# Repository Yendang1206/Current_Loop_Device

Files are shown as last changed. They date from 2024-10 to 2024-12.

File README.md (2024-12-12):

# Digital Current Loop Device for Frequency Converters
This repository contains the design and implementation details of a digital current loop device for frequency converters, developed as part of a thesis project. This device serves as an intermediate unit between a motor and a frequency converter, featuring advanced functionalities such as fast and slow increments or decrements for user-friendly control.
## Overview
The digital current loop device converts digital inputs—representing torque (0–50 Nm) and speed (0–3000 rpm)—into 0–20 mA analog current loops. This project integrates hardware and software to achieve precise control, accurate signal processing, and robust performance in noisy environments.
## Key Features
+ Converts torque and speed inputs from a rotary encoder into 0–20 mA current loop outputs.
+ Displays real-time input values on an LCD I2C screen.
+ Offers convenient fast/slow increment and decrement control.
+ Incorporates grounding, shielding, and paired signal wiring to enhance signal stability.
## The work methods
The work methods for this project were split into three main stages: 
 + circuit design, simulation and prototyping,
 + developing an Arduino software program,
 + manufacturing the physical Printed Circuit Boards (PCB).
## Results
Demonstrated positive correlation between torque and speed inputs with the corresponding current loop values (0–20 mA).
Achieved consistent performance between breadboard prototypes and integrated PCB systems.
Eliminated capacitive crosstalk and frequency interference using proper grounding, shielding, and CAT6 cable pairing.
## How to use
1. Connect the device between the motor and the frequency converter.
2. Adjust torque and speed inputs using the rotary encoder.
3. Monitor real-time input values on the LCD I2C display.
4. Verify current loop outputs using multimeters for accuracy.
## Future recommendations
Conduct EMC testing to further enhance noise immunity and long-term stability.

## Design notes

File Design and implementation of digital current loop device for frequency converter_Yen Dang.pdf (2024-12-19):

Yen Dang

# DESIGN AND IMPLEMENTATION

# OF DIGITAL CURRENT LOOP DEVICE

# FOR FREQUENCY CONVERTER

School of Technology
2024

VAASAN AMMATTIKORKEAKOULU
UNIVERSITY OF APPLIED SCIENCES Information Technology

ABSTRACT

Author | Yen Dang
Title | Design and Implementation of Digital Current Loop
| Device for Frequency Converter
Year | 2024
Language | English
Pages | 49
Name of Supervisor Jani Ahvonen

This thesis focuses on the design and implementation of a digital current loop device for a frequency converter to serve as an intermediate device between the motor and the frequency converter. In addition, this current loop device has an advanced feature of fast and slow increments or decrements, which is very convenient and user-friendly for users.

The work methods for this project were split into three main stages: circuit design and prototyping, Arduino software development and manufacturing the physical Printed Circuit Boards (PCB) for the digital current loop device. The expected inputs such as torque (Nm) and speed (rpm) values were fed into a rotary encoder and were displayed on an LCD I2C screen simultaneously. Then, the digital inputs for the torque (0 – 50 Nm) and for the speed (0 – 3000 rpm) were converted into the 0 – 20 mA current loops through DACs connected to the Arduino Nano board. In addition, the prototype measurement was divided into four main parts: Filter, Digital Signal Processing, Digital Analog Converter (DAC) and Analog to Digital Converter (ADC). These individual circuits on breadboards were verified with the software program simultaneously to achieve the accurate outcomes before integrating them together.

The results from the integrated PCBs were consistent with the individual circuit initially tested on the breadboards. Consequently, the desired torque and speed values showed positive correlations with the corresponding current values ranging from 0 – 20 mA. The finished device was assembled by placing PCBs into two metal boxes connected via CAT6 cable. To ensure accuracy and eliminate the capacitive crosstalk issue and frequency interference, signal wires were paired and proper grounding and shielding techniques were implemented. These measures were crucial for maintaining signal stability in potentially noisy environments, ultimately enhancing the accuracy of the 0 – 20 mA current loop outputs.

Keywords | Encoder, LCD I2C, Arduino Nano, DAC, current loop, ADC, digital
| current loop device, frequency converter

CONTENTS

6 TESTING AND TROUBLESHOOTING THE PROTOTYPE ON BREADBOARDS ..... 32

8.2 Comparative Analysis of Output Results of Ten Devices and Main

LIST OF TABLES

Table 1. Encoder logic state | 16
Table 2. Lookup table of the encoder changes | 28
Table 3. Error measurement range for actual current values | 43

LIST OF FIGURES

Figure 1. The hardware block diagram | 7
Figure 2. The flowchart software diagram | 8
Figure 3. Quadrature output table | 15
Figure 4. The external voltage circuit drawn in LTspice | 17
Figure 5. Simulation of the external voltage from the TL431 chip | 18
Figure 6. The simplified transmitter circuit drawn in LTspice | 20
Figure 7. Simulation of the simplified transmitter circuit | 20

Figure 8. The simulating receiver and feedback loop circuits drawn in LTspice. . 21

Figure 9. Simulation of the simulating receiver and feedback loop circuits | 22
Figure 10. The filter circuit’s schematic | 23
Figure 11. The main board circuit’s schematic | 24
Figure 12. The encoderLCD circuit’s schematic | 25
Figure 13. The appropriate libraries | 25
Figure 14. The calibrations for ADC and DAC for both channels | 26

Figure 15. Updating the torque and speed changes through the function of void

write_dac(float torque, int rpm) | 26
Figure 16. The state of a push-button | 27
Figure 17. The state of the encoder changes as an external interrupt | 27
Figure 18. Fast or slow increments featuring for four steps forward | 29
Figure 19. Safety checks within defined limits | 29
Figure 20. Open loop error check featuring | 30
Figure 21. I2C network | 31

Figure 21. The main components of the prototype testing on breadboards....... 32

Figure 23. The filter’s PCB | 34

Figure 29. Setup for testing the finished device with the frequency converter... 40

Figure 31. EMI shielding tapes applied to the CAT6 cable and EMC conductors

### 1 INTRODUCTION

The objective of the thesis is to design and implement a digital 0 – 20 mA device

for frequency converter. Users can adjust the expected values such as torque and

speed values on an LCD by rotating an encoder. The design of this device is illus-

trated through hardware and software diagrams.

### 1.1 Block Hardware Diagram

The hardware block diagram of the device is designed as shown below.

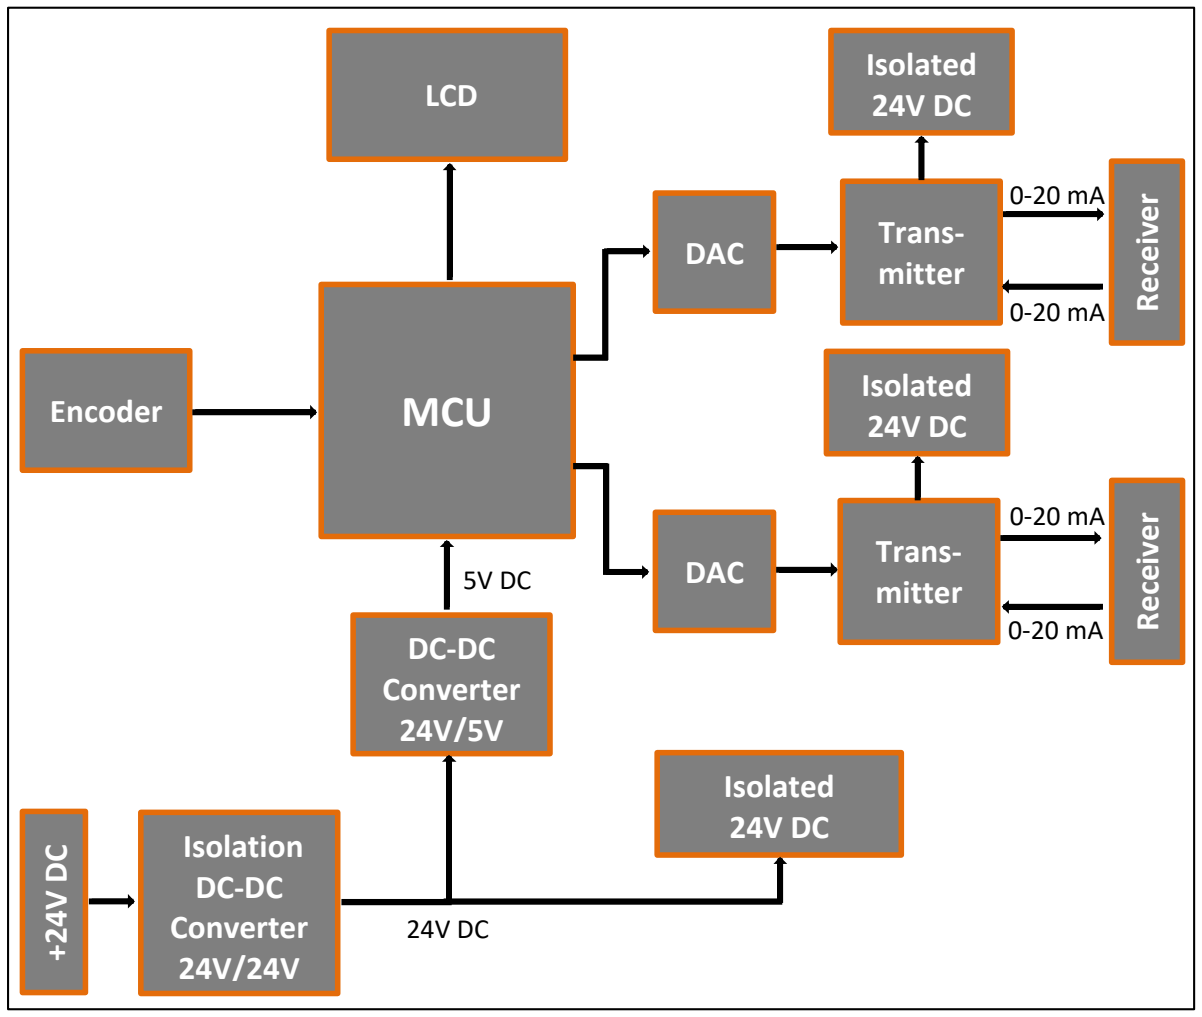
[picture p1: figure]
MCU; Trans- mitter; Encoder; DC-DC Converter 24V/5V; Isolation DC-DC Converter 24V/24V; DAC; LCD; Receiver Receiver; Isolated 24V DC

Figure 1. The hardware block diagram

Shown in the diagram, the encoder would be used to set the desired current value

by users. The desired digital value would be fed into MCU. Then, MCU would pro-

cess the data by displaying it on the LCD screen. MCU would send the desired dig-

ital value to a DAC. The DAC would convert the digital data back into the analog format. The analog output from DAC would control the current levels in the cur-

rent loops (transmitter and receiver).

### 1.2 Flowchart Software Diagram

The program for the device is presented in Figure 2.

Figure 2. The flowchart software diagram.

The main loop comprisesfive functionssuch as reset watchdog, check errors, write

text and values to LCD, write values to DACs and print all values to terminal. Each

of these fuctions has the specific internal behaviour within the system. The reset

watchdog serves as a critical safety mechanism by periodically resetting the watchdog timer to prevent the system from freezes or hangs, thus ensuring con-

tinuous operation. It acts as a fail-safe to automatically restart the system if it be-

comes unresponsive. Next, the check errors function continuously monitors the

system for any potential errors by comparing the desired torque and rpm values

with their corresponding ADC feedback. It returns a combined error code: 1 for a

torque channel error, 2 for an rpm channel error, or 3 if both channels have errors.

Another crucial function is the write text and values to LCD, which updates the

user interface by displaying relevant errors, torque, and rpm values on the LCD

screen. It provides users with real-time information about the system's status and

operation. Furthermore, the write values to DACs function converts digital signals

to analog outputs through DACs. It calculates new DAC values when the changes

occur, then updates the appropriate channels based on the values of the global

DAC_select variable. Lastly, the print all values to terminal function outputs all rel-

evant system values and information to a terminal interface. It is essential for de-

bugging and monitoring purposes, allowing users or operators to access detailed

system data in real-time.

### 2 REQUIREMENT SPECIFICATION

### 2.1 Functional Requirements

For the current control, the desired current level is adjusted within the range of 0

– 20 mA by turning the knob of the encoder.

For LCD screen, it should display the desired current level adjusted by users.

For the response time, the device should have a fast response time to quickly and

accurately adjust the current level.

### 2.2 Requirements for Interfaces

As for the user interface, the device should contain the LCD display and the rotary

encoder, which can be used to display and turn a knob to achieve the expected

digital values, respectively.

For hardware interface, the device should be able to rotate the encoder manually

to achieve the desired values displayed on the LCD display. Additionally, the device

contains two current loop outputs that can be directly connected to the analog

inputs of a frequency converter. The use of current loop outputs enables for pre-

cise control and communication between the device and the converter, allowing

real-time data transmission for adjusting accurate parameters such as torque and

speed.

For software interface, the device should allow users to control torque and speed

value setpoints. Moreover, the device should have a function to detect errors

when any open loops occur.

In terms of communication, the device could be programmed via serial communi-

cation through MCU’s USB port. This allows the MCU to transfer data to the com-

puter. The serial communication port is fixed, so there is no need to modify the

setting.

### 2.3 Other Requirements

### 2.3.1 Performance Requirements

There are some requirements for the device’s performance, as follows:

- Resolution of measurement: 0.02 mA
- Range of measurement: 0 – 20 mA

### 2.3.2 Usability Requirements

The device should have a user-friendly design, without the requirements for any

specialized skills.

### 2.3.3 Safety Requirements

The device must be protected with a fuse to prevent damage from overcurrent or

electrical faults.

### 2.3.4 Maintenance Requirements

The maintenance requirements include a more robust and user-friendly digital 0 –

20 mA device that can be monitored remotely and facilitates efficient trouble-

shooting and repairs if needed. This approach would help users to ensure its long-

term system performance and reliability, reduce the risk of unexpected outputs as

well.

### 2.3.5 Portability and Compatibility Requirements

Frequency converters play a crucial role in a variety of fields in daily life such as

control systems, power electronics, robotics, and automation, so the digital cur-

rent loop device would be used with various types of frequency converters. There-

fore, both portability and compatibility characteristics should be considered.

- For the portability factor, the designed device should be lightweight and

small for ease of installation.

- For the compatibility element, the digital current loop device could be able

to communicate with different types of communication interfaces when

integrated with a wide range of frequency converters.

### 2.3.6 Environmental Requirements

The device must operate within the temperature range from −30°C to +30°C to

ensure the desired functionality.

Furthermore, the device must operate its own environment as designed. Moreo-

ver, the device must comply with proper EMC regulations to minimize any poten-

tial interferences and noise.

### 2.4 Restrictions of Design

### 2.4.1 Restrictions caused by previously used technologies

The device must be very simple, so it can use MCU Arduino Nano A000005 board

schematic as a basic of design /3/.

The digital 0 – 20 mA device requires the existing industrial systems and control

devices to have the 0 – 20 mA input terminals. This is because in the real world,

the 0 – 20 mA or 4 – 20 mA current loops have commonly used as the standard for

signal transmission and electronic control in many industries /16/.

### 2.4.2 Hardware Limitations

The physical device should be as small as possible.

With a 0 mA current signal, it might be difficult to detect the system failures /14/.

Moreover, the wire loop distance between the transmitter and the receiver should

be within 500 meters.

### 2.4.3 Software Restrictions

The software for this project would be written in the C language, so only the GCC

C-compilers are permitted for developing this program.

### 2.4.4 Other Limitations

The power consumption should be minimized as much as possible while ensuring

the whole system has sufficient power to operate smoothly.

In addition, ground loops might be an unpredictable problem to crash the system.

This is because when many grounded devices placed in different locations are in-

tegrated with each other, which might have different voltage potentials, the noise

injection generated from their ground connection might affect grounded devices.

Therefore, we assumed all grounded components would be placed at the same

ground point to prevent the ground loops /15/.

### 3 OVERVIEW OF FREQUENCY CONVERTERS

A frequency converter is known as a variable frequency drive or adjustable speed

drive, which is used for modifying and controlling the speed and torque of electric

motors. Initially, this device converts the alternating current (AC) voltage into di-

rect current (DC) voltage. Then, it reconverts this DC back into AC with adjustable

frequency and the levels of voltage. This process allows for precise control over

the motor’s performance, enabling it to operate at the desired torque and rota-

tional speed required for the motor.

In addition, frequency converters can reduce motor power consumption by up to

50%, leading to significant energy savings. Moreover, they can collect motor data

such as temperature and vibrations via sensors, enabling condition monitoring and

preventive maintenance. This allows for remote operation monitoring and trou-

bleshooting through cloud solutions. Therefore, these advantages make frequency

converters essential devices in modern industrial applications, offering improved

performance, efficiency and control across a wide range of sectors.

However, frequency converters can create different kinds of interference when

assembled directly to motors or connected via cables. This includes acoustic noise,

harmonic reactions on the network, and electromagnetic compatibility (EMC)

noise, which can affect radio devices and data transfers. Therefore, the installation

of frequency converters and motors should address and manage noise and inter-

ference by complying with EMC requirements /12/.

### 4 BACKGROUND THEORY

### 4.1 Digital Signal Processing

In the implementation of the digital current loop device, we manipulate the digital

desired inputs from the rotary encoder and then convert them to analog signals

for transmission to the frequency converter. To ensure accurate tracking and fa-

cilitate real-time adjustments, we have integrated an I2C LCD 1602 display in this

project. This display serves as a visual interface, presenting the desired digital in-

put signals in a clear and easily readable format, allowing for quick identification

of any discrepancies or issues that may arise during operation. Therefore, this fea-

ture is useful for users to monitor the system's performance continuously when

there are any changes in the wanted digital inputs from the encoder.

### 4.1.1 Rotary Encoder

In the project, the rotary encoder is an incremental encoder, which is PEC11R-

4220F-S0024. This encoder converts angular motion or position of a shaft into an

analog or digital code to determine position or motion /8/. This encoder creates a

specified number of pulses per rotation. There are two output channels of pulses

such as Channel A and Channel B, which are offset from each other to indicate the

direction of rotation. The phase relationship between these channels is known as

quadrature. When the encoder is rotated in a clockwise direction (CW), Channel A

is leading Channel B in the output signal sequence. In contrast, during counter-

clockwise (CCW) rotation, the signal sequence reverses, meaning Channel B is

leading Channel A. The quadrature output table is represented as below /6/.

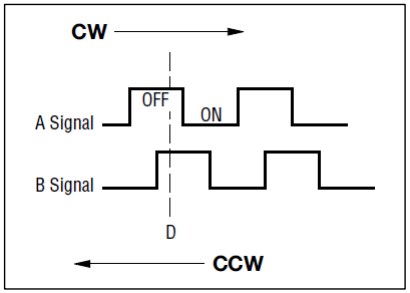
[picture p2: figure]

Figure 3. Quadrature output table.

Based on the quadrature output table, we could derive a encoder logic state table,

which is illustrated as Table 1.

Table 1. Encoder logic state.

Clockwise Direction

Position | Channel A | Channel B
1 | 0 | 0
2 | 1 | 0
3 | 1 | 1
4 | 0 | 1

In addition, this encoder is integrated with an additional feature, which is a push

switch option. The push button is often used to trigger of specific actions or toggle

between different operational modes.

### 4.1.2 I2C LCD1602

An I2C LCD1602 is a display device that combines a standard LCD (Liquid Crystal

Display) and an I2C (Inter-Integrated Circuit) module attached to its backside. This

device could show text and characters on 2 rows with 16 columns. One of the key

advantages of the I2C LCD1602 lies in its simplified connection interface. Unlike

traditional LCDs that often require multiple pins for operation, this device utilizes

only four pins: GND (ground), VCC (power supply), SDA (Serial Data), and SCL (Se-

rial Clock). This configuration simplifies the wiring process /5/.

### 4.2 Digital-Analog Converter

The Digital-Analog Converter (DAC) is a device that converts a digital input signal

into an analog output signal. Specifically, the DAC transforms the binary signal in

the form of bits into an analog voltage or current. The DACs find widespread ap-

plicationsin various digital signal processing fields, including audio amplifier, video

encoder, display electronics, data acquisition systems and motor control /7/.

In this thesis, we utilized two DFRobot Gravity 12-Bit I2C DAC modules equipped

with EEPROM (Electrically Erasable Programmable Read-Only Memory) to facili-

tate the conversion of digital input signalsfrom the encoder into voltage or current

signals suitable for the frequency converter. These DAC modules incorporate a 12-

bit DAC MCP4725 chip,support a wide input voltage range of 3.3 – 5 V and include

an I2C address selection switch. The integration of EEPROM in these DAC modules

significantly enhances data retention and system reliability. This non-volatile

memory component could retain the DAC input values while the power is turned-

off and resume the DAC output upon power resumption /7/.

Moreover, the input voltage for DAC modules was chosen at 5 V. Instead of using

the internal voltage of Arduino Nano, we chose for an external voltage circuit, aim-

ing for more stable and precise values for the whole system. Therefore, we used

the reference chip of TL431, namely Adjustable precision Zener shunt regulator,

to generate a constant output voltage at 5 V, a reference voltage for both DACs

and Arduino Nano. The circuit of the external voltage was designed in LTspice, as

shown in Figure 4.

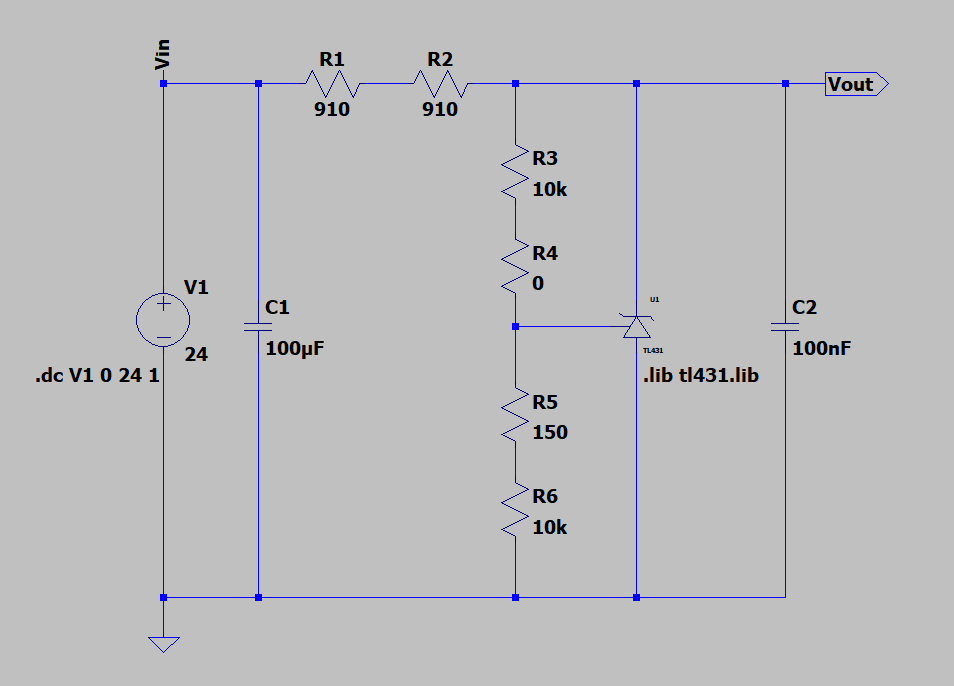
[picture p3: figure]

Figure 4. The external voltage circuit drawn in LTspice.

The circuit was then simulated as shown in the picture below. The results indicated

that the input voltage of 24 V, serving as the voltage source, was successfully con-

verted to the constant output voltage of 5 V.

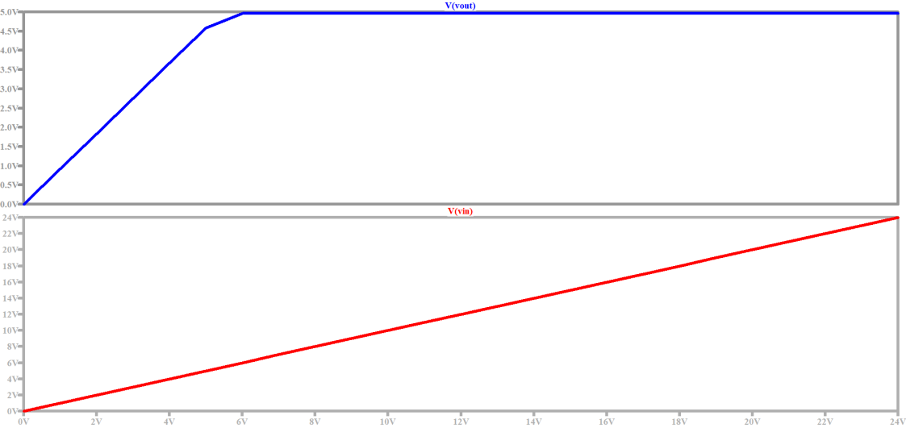
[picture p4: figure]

Figure 5. Simulation of the external voltage from the TL431 chip.

### 4.3 Current Loop

### 4.3.1 Transmitter Circuit

After converting the digital input signals to the analog signals, we connected the

analog output to a transmitter circuit for converting the input voltage into an out-

put current. The transmitter circuit incorporates two key components: an opera-

tional amplifier (LM324) and a transistor (BC547).

The LM324 operational amplifier was utilized for maintaining signal integrity and

ensuring that even small voltage changes are accurately represented in the output

current. The LM324 series feature cost-effective quad operational amplifiers with

true differential inputs, designed for single supply operation within a 3.0 – 32 V

range. The amplifier offerslow quiescent currents and numerous advantages such

asshort-circuit protection, true differential input stages. Moreover, the LM324 se-

ries also provides low input bias currents, internal compensation, and a common

mode range extending to the negative supply. With industry-standard pinouts and

ESD (Electrostatic Discharge) protection, these versatile amplifiers suit various ap-

plications requiring reliable operation /13/.

Following the amplifying stage, we used the BC547 Bipolar Junction Transistor

(BJT), which is used for amplifying current or switching. The transistor has three

regions: emitter, base, and collector. By controlling the base current, the transistor

can be turned on or off, allowing a larger current to flow between the collector

and emitter. This property makes it useful for amplifying small signals or acting as

a switch. The BC547 is popular due to its affordability, availability, and ease of use

/10/. Hence, this BC547 was used to generate the 0 – 20 mA output current in our

device.

The simplified transmitter circuit applied in this project in Figure 6.

Figure 6. The simplified transmitter circuit drawn in LTspice.

In addition, we also simulated the transmitter circuit above to measure the output

current of transmitter and the output voltage of receiver. After simulating, within

the input voltage range of 0 – 5 V, the transmitter output current was from 0 mA

to 20 mA and the receiver output voltage was from 0 V to 5 V. These results were

shown in Figure 7 below.

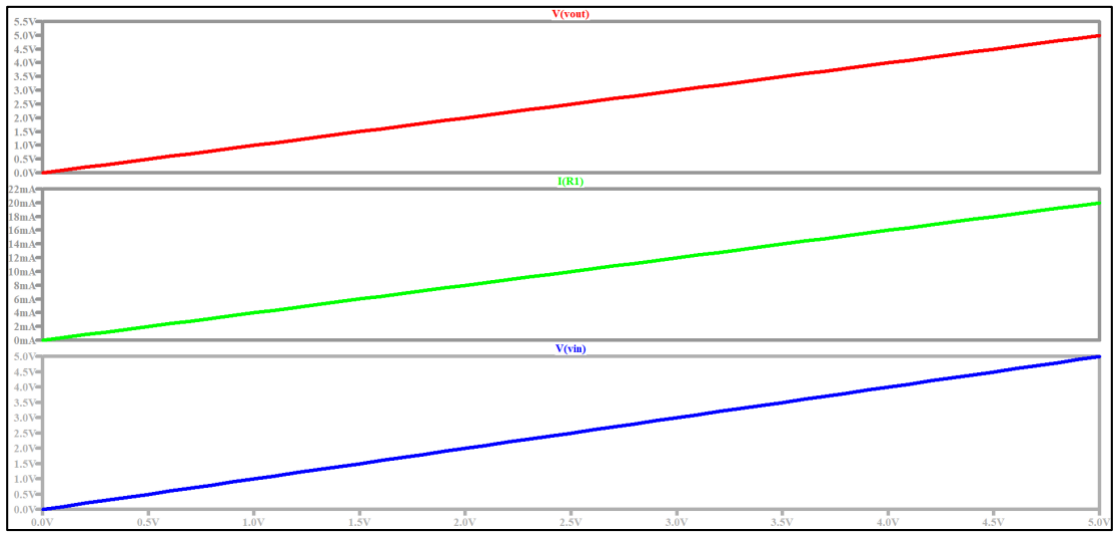
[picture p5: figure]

Figure 7. Simulation of the simplified transmitter circuit.

### 4.3.2 Feedback Loop Circuit

To complete the current loop, we implemented a feedback loop circuit designed

to capture and process the transmitted current signal. This circuit performs the

essential function of converting the received current back into its original voltage

form, enabling further processing or utilization of the signal. This circuit consisted of two main parts such as a resistor of 250 Ohm simulating frequency converter or

receivers and the feedback loop. To be specific, the feedback loop incorporated

three main parts: the low pass filter cut-off frequency, two diodes of 1N4148 for

ESD protection and a resistor of 250 Ohm.

Firstly, the low pass filter part consisted of a resistor of 10 kOhm, and a capacitor

of 100 nF for filtering out frequencies above the cut-off point. The cut-off fre-

quency was calculated following the below formula:

fc =

1
2πRC =

1
2π ∗ 10kΩ ∗ 100nF = 159.1 Hz ≈ 0.16 kHz

This calculated cut-off frequency of approximately 0.16 kHz ensured that the cir-

cuit effectively attenuates signals above this threshold, resulting in a more stable

output signal.

Secondly, these diodes of 1N4148 acted as a safeguard, protecting the sensitive

components of the circuit from potentially damaging voltage spikes that might oc-

cur due to static electricity or other sources.

Lastly, the receiver circuit included the resistor of 250 Ohm to control and main-

tain the targeted current output signals, preserving the 0 – 20 mA current flow

transmitted from the transmitter circuit and the receiver.

Here is the simulating receiver (the resistor of 250 Ohm) and feedback loop circuit

shown as below.

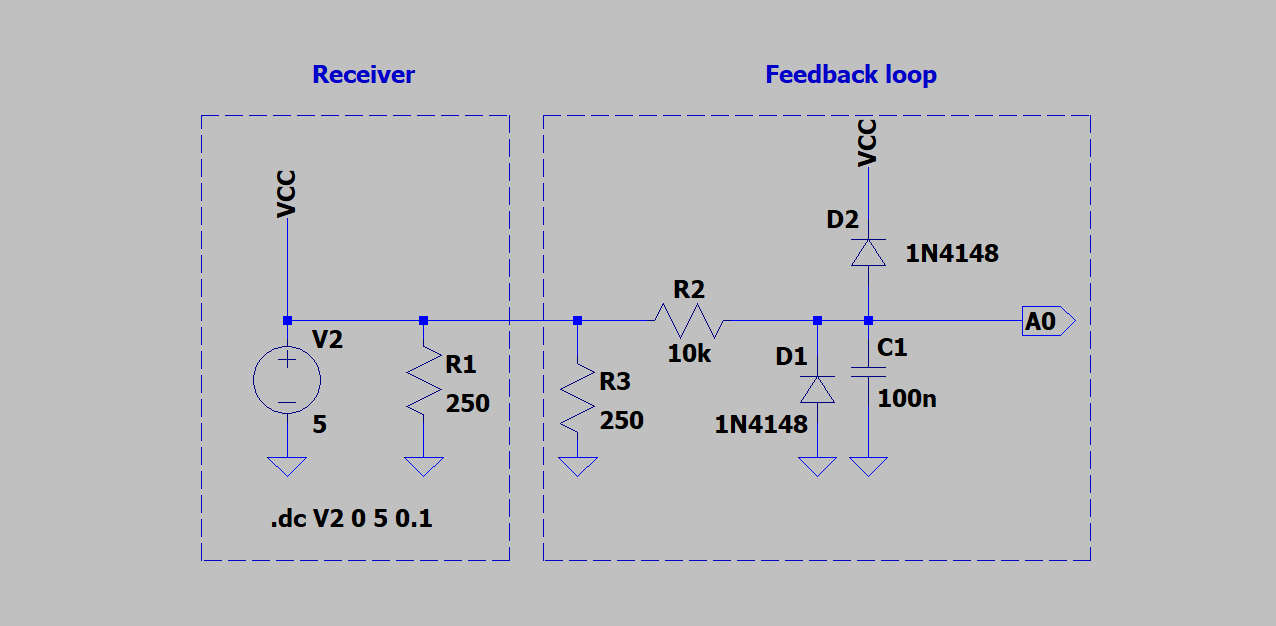
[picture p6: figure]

Figure 8. The simulating receiver and feedback loop circuits drawn in LTspice.

The simulation results from this simulating receiver and feedback loop circuits

were shown as Figure 9 below. The figure illustrated that the current value going

through R1 represented as the receiver or the frequency converter was from 0 –

20 mA. In addition, the 0 – 20 mA current flow was transmitted to the feedback

loop. Then, this current flow was converted into the output voltage of 5 V.

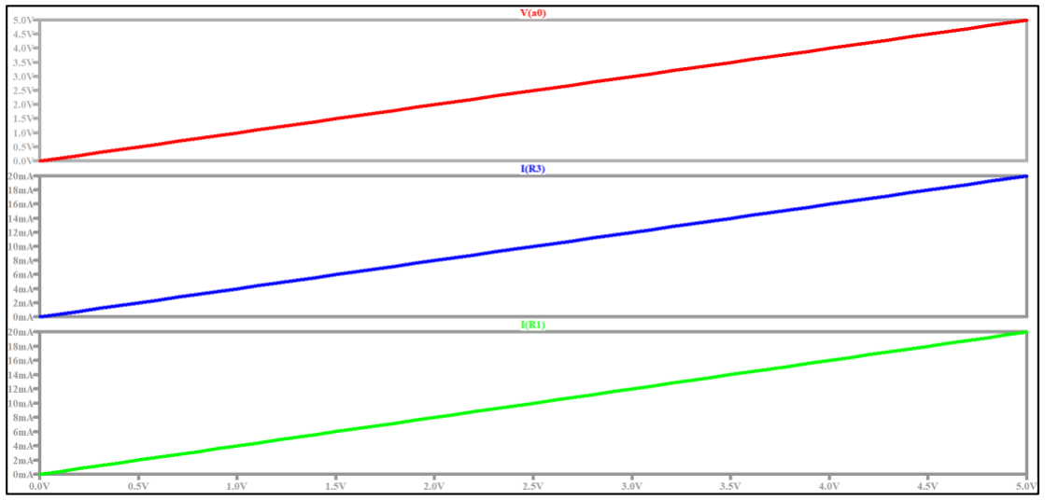
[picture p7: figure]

Figure 9. Simulation of the simulating receiver and feedback loop circuits.

### 5 SCHEMATICS AND IMPLEMENTATION

The project’s schematics were divided into two main parts, including a main board

schematic and a digital signal processing schematic. The digital signal processing

circuit included the encoder and LCD circuits. The remaining circuits including a

filter, external reference voltage, DACs, transmitter and feedback loop circuits

connected to Arduino Nano belonged to the main board schematic.

### 5.1 Schematics

The filter circuit’s schematic was designed as below:

Figure 10. The filter circuit’s schematic.

The main board circuit’s schematic was designed as below:

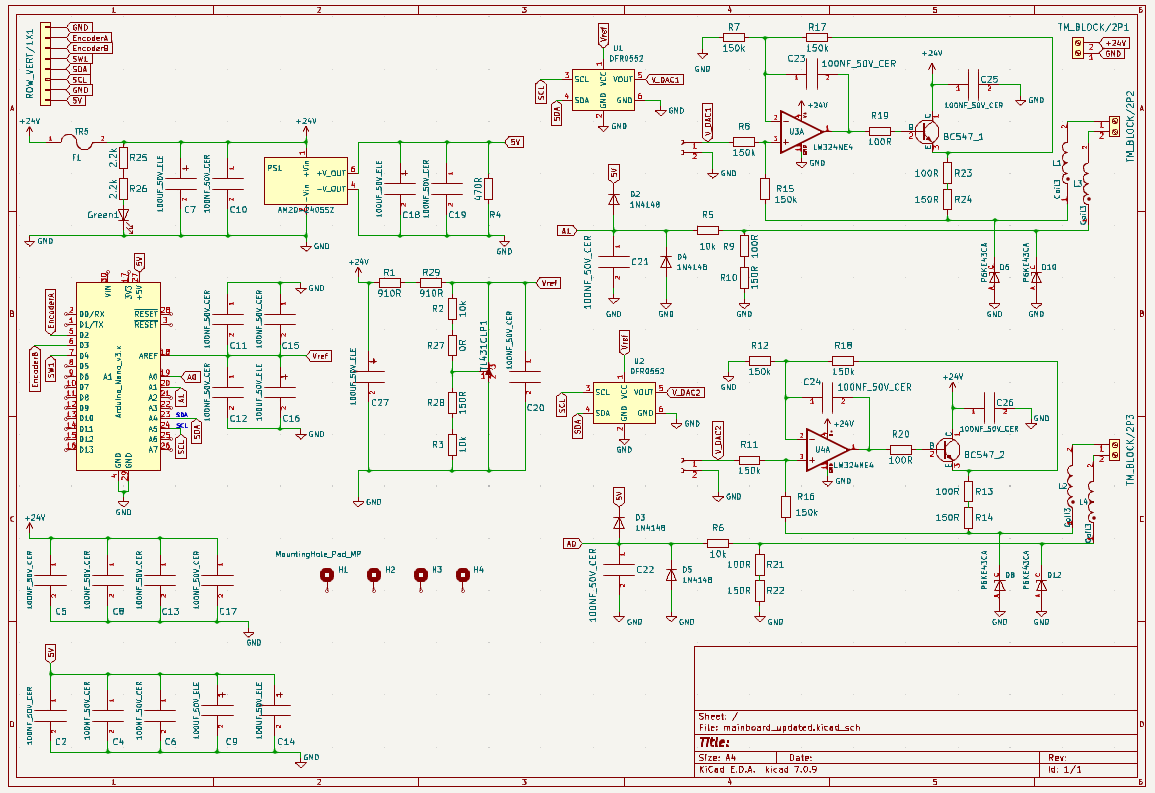
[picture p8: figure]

Figure 11. The main board circuit’s schematic.

The encoderLCD circuit’s schematic was designed as below:

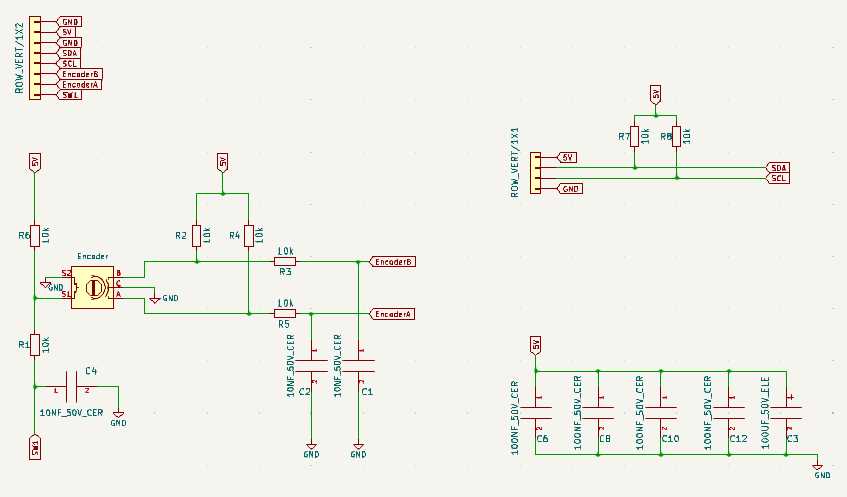
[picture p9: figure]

Figure 12. The encoderLCD circuit’s schematic.

### 5.2 Software Implementation

This project built up the device with two channels of 0 – 20 mA current loop using

Arduino software program. The implementation involved setting up and control-

ling a system with the LCD display, two DACs, the rotary encoder including two

main external interrupts, feedback loops and ADC. Additionally, a watchdog timer

is implemented to reset the system if it becomes unresponsive. Initially, we

needed to install the appropriate libraries used in this project.

Figure 13. The appropriate libraries.

To address inaccuracies in the DAC's reference voltage, we set a calibration value

to achieve a more precise output voltage. Our target was 5 V for each DAC when

achieving the current value at 20 mA, resulting in a calibration value of 5000 milli-

volts:

Calibration of DAC = 5*1000 = 5000

In addition, the calibration ensures precise conversion between analog and digital

values throughout the system. Due to Arduino Nano offers a 10-bit resolution ADC

for analog pins, the calibration of ADC could be calculated as below.

Calibration of ADC = 2

10 − 1 = 1023

These calibrations were defined in the software as follows:

Figure 14. The calibrations for ADC and DAC for both channels.

In this program, every change of the torque and speed values by using the encoder

are updated through the function of void write_dac(float torgue, int rpm). In

other words, this function calculates new DAC values when there are any changes

occuring, then updates the appropriate channels.

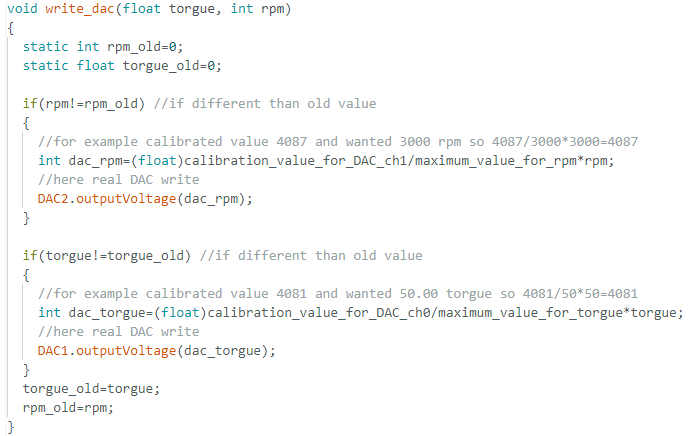
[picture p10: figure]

Figure 15. Updating the torque and speed changes through the function of void

write_dac(float torque, int rpm).

The encoder has two functions such as push-button and changing encoder states

when controlling the desired input values. In this project, the

void read_push_button_state(void) function manages the state of a push-button from the encoder. It uses a static variable ‘timex’ for 200 ms debouncing to avoid

multiple triggers from one press. When the button is pressed (indicated by digi-

talRead(SW_PIN) = = 0), and the debounce time has passed, it toggles the DAC_se-

lect variable between true and false, switching between DAC1 and DAC2.

The timex variable is then updated to the current time using millis() for accurate

debouncing in subsequent presses.

Figure 16. The state of a push-button.

An external interrup is the void ISR_encoderChange(void) function, which is

responsible for processing the changes of the encoder’s state to modify the torque

and rpm values. Here is a part of this function shown in Figure 17. In this function,

we used a lookup table of the encoder state to determine the rotation direction

such as a clokcwise direction (CW) or a counterclockwise direction (CCW).

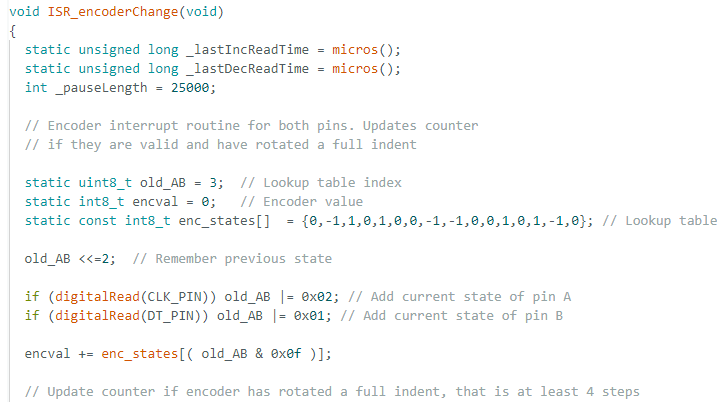
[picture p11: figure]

Figure 17. The state of the encoder changes as an external interrupt.

Due to the encoder has two outputs, generating four possible states: 00, 01, 10

and 11, the lookup table could be represented as below:

Table 2. Lookup table of the encoder changes.

Previous State | Current State | Index (Binary) | Index (Decimal) | Change
00 | 00 | 0000 | 0 | 0
00 | 01 | 0001 | 1 | -1
00 | 10 | 0010 | 2 | 1
00 | 11 | 0011 | 3 | 0
01 | 00 | 0100 | 4 | 1
01 | 01 | 0101 | 5 | 0
01 | 10 | 0110 | 6 | 0
01 | 11 | 0111 | 7 | -1
10 | 00 | 1000 | 8 | -1
10 | 01 | 1001 | 9 | 0
10 | 10 | 1010 | 10 | 0
10 | 11 | 1011 | 11 | 1
11 | 00 | 1100 | 12 | 0
11 | 01 | 1101 | 13 | 1
11 | 10 | 1110 | 14 | -1
11 | 11 | 1111 | 15 | 0

Furthermore, this function implementes a feature of fast or slow increments or

decrements based on the time elapsed since the last change, ensuring smooth and

responsive adjustments. The Figure 18 illustrates an example of the feature of fast

or slow increments for four step forward.

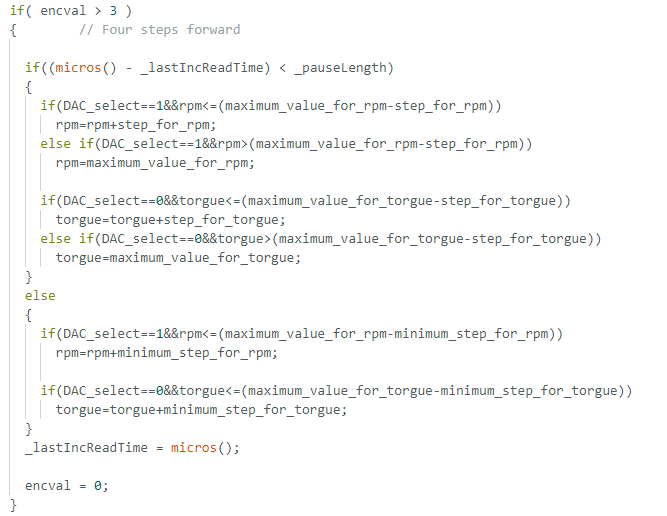
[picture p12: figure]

Figure 18. Fast or slow increments featuring for four steps forward.

Additionally, the software program is also included safety checks to keep the

torque and rpm values within their defined limits.

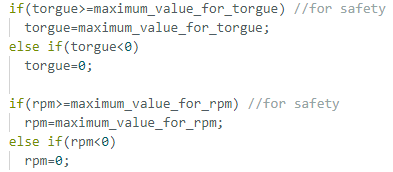
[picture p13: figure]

Figure 19. Safety checks within defined limits.

Besides, we also added one function for detecting possible errors in a control

system by comparing the desired torque and rpm values with their corresponding

ADC feedbacks, which was int open_loop_error_check(void) as follows. For

torque values, it flags an error if the desired value exceeds approximately 100

while the feedback is below 20. A similar check is performed for rpm. The function

returns a combined error code: 1 for a torque channel error, 2 for an rpm channel

error, or 3 if both channels have errors. This error checking mechanism helps

identify potential issues in the open loop control system, such as disconnections.

Figure 20. Open loop error check featuring.

### 5.3 I2C Communication Protocol

For data communication and transfer in this project, we leveraged the I2C (Inter-

Integrated Circuit) protocol. This choice was particularly apt as key components of

our system - namely the DAC DFR0552, I2C LCD, and Arduino Nano - all support

I2C addressing, allowing for integration.

The I2C protocol is a serial communication protocol that uses two wires: SDA (Se-

rial Data) and SCL (Serial Clock), simplifying the wiring and reducing the number of

pins required. This protocol is used for communication between a master or con-

troller (or multiple masters) and a single or multiple slave devices. The SDA line

carries the actual data being transmitted, while the SCL line provides the clock sig-

nal that synchronizes the data transfer. Here is an example of I2C network in Figure

21 /17/.

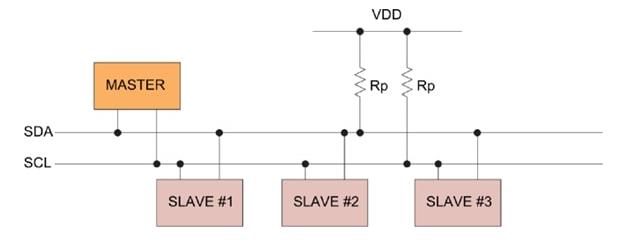
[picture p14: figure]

Figure 21. I2C network.

### 6 TESTING AND TROUBLESHOOTING THE PROTOTYPE ON BREAD-

BOARDS

As our project evolved, we continually refined and enhanced our software to ad-

dress increasingly sophisticated requirements dictated by the evolving prototype

design. In the initial stages of development, our primary focus was on creating

software capable of generating a precise output current of 20 mA and a voltage of

5 V. These parameters formed the foundation of our early prototyping efforts and

served as the baseline for our initial testing phase. Consequently, when we con-

ducted our preliminary evaluations using breadboards, we utilized this initial ver-

sion of the software to power and control the prototype.

To ensure the reliability and accuracy of our design, we embarked on a thorough

testing phase. This involved constructing and evaluating the critical components

of both the main board and the encoderLCD circuits. We utilized breadboards for

this purpose, as they provided an ideal platform for prototype testing. Our main

goal was to verify if the actual output results matched our expected outcomes and

simulation results in LTspice. We also aimed to ensure these results were accu-

rately displayed on the LCD interface, which was crucial for user interaction and

system monitoring. Here are the main components of the prototype tested on

breadboards.

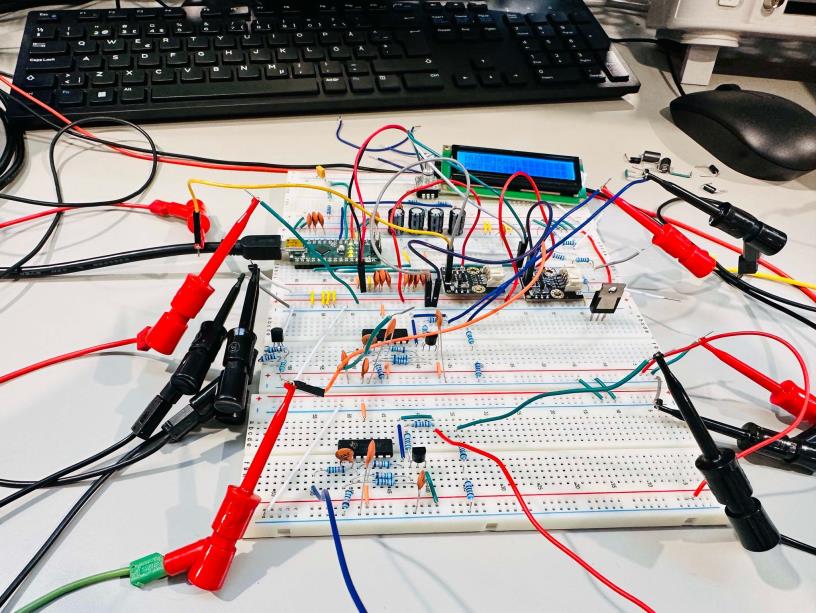
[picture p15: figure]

Figure 22. The main components of the prototype testing on breadboards.

During the testing phase, we encountered several significant issues that required

careful attention and resolution. One of the primary challenges we faced was re-

lated to ground connections. We discovered it was crucial to connect all ground

points together to effectively eliminate ground noise and achieve more accurate

outputs. This realization came after a costly learning experience in our initial test-

ing rounds. After three DACs were broken or burned, we found that interference

from ground points made the input voltages of the DACs abnormal. This occurred

because the output grounds of the DACs were not connected to other ground

points, and the grounds of each breadboard were not linked together. Conse-

quently, the DACs' output voltages were out of the operational range required in

the datasheet. As a result of this incident, we properly connected all ground points

in the prototype to create a stable reference point for our circuits.

After addressing this issue, the final output values were still higher than our calcu-

lated values, and another DAC was broken. We found that noise generated within

the breadboards was the main cause of this problem. When we tested the proto-

type with the reference voltage created by the TL431 chip, the output values were

much higher than expected, contradicting the simulation results. However, by us-

ing a 5 V external power supply as the reference voltage, the output results were

closer to the expected values.

Consequently, after conducting thorough testing and troubleshooting procedures

as above, we recognized the need for a more stable and reliable platform for our

prototype. This prompted us to initiate the process of designing PCB layouts.

### 7 DESIGN AND MANUFACTURE OF PRINTED CIRCUIT BOARDS

Our transition to PCBs was driven by the need for a more stable, noise-resistant

platform than the breadboards we had been using. This crucial step in our devel-

opment process ensured the reliability of the entire system design.

In this prototype, we designed and manufactured three distinct printed circuit

boards (PCBs) based on the three comprehensive schematics mentioned earlier.

This approach optimized the layout and functionality of each circuit, maximizing

efficiency and performance in a finished product.

### 7.1 Design PCB layouts

### 7.1.1 The Filter’s PCB

The filter’s PCB was designed as below:

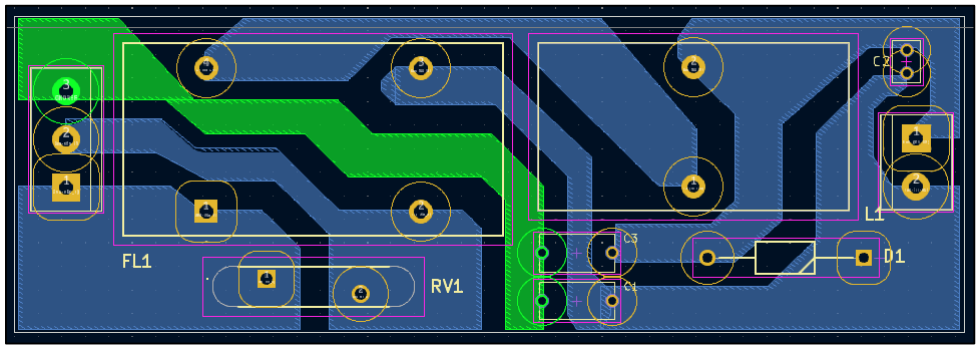
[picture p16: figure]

Figure 23. The filter’s PCB.

### 7.1.2 The Main Board’s PCB

We designed a PCB for the main board part in two layers by using both SMD and

through hold components.

A critical aspect of our design process involved thorough thermal analysis. To mit-

igate the risk of component overheating, we conducted detailed power consump-

tion calculations for resistors. Our benchmark for thermal safety was set at a con-

servative one-fifth of the maximum rated power consumption for some resistors.

In this device, through-hole resistors have 600 mW and SMD resistors have 250 mW according to the power consumption indicated by the manufacturers. Hence,

we could calculate the maximum rated power consumption for through-hole and

SMD resistors:

The maximum rated power consumption for through-hole resistor:

P1 =

600
5

= 120 mW

The maximum rated power consumption for SMD resistor:

P2 =

250
5

= 50 mW

If the real power consumption is smaller or equal to P1 and bigger than P2, the

resistor should be through-hole.

Here is the PCB layout of the main board.

Figure 24. The mainboard’s PCB.

### 7.1.3 The EncoderLCD’s PCB

The PCB of the encoderLCD circuit was designed in one layer.

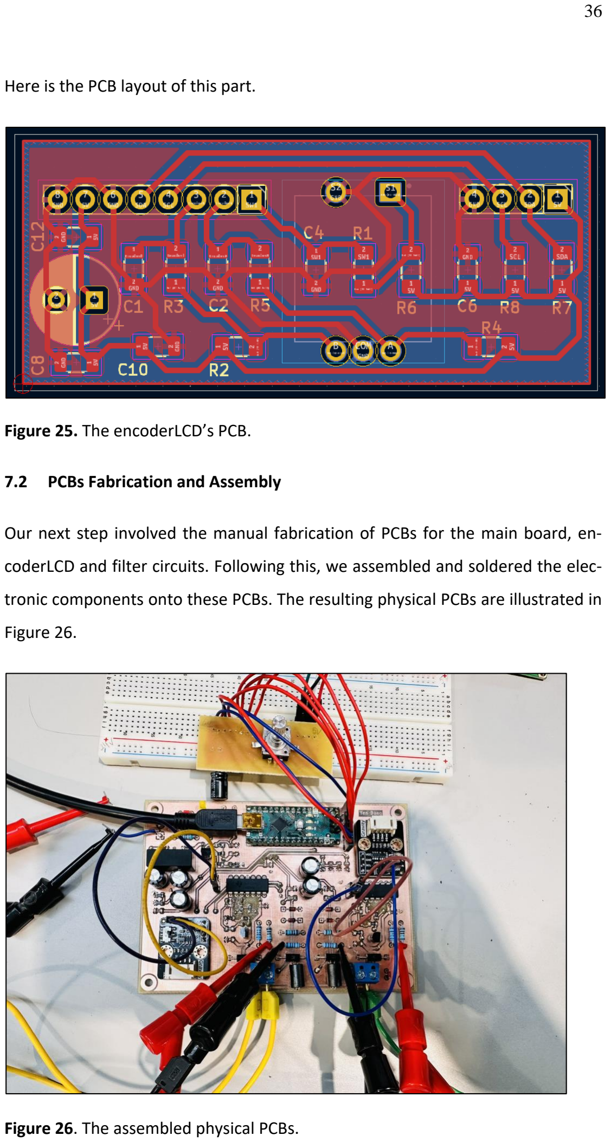
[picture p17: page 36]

Here is the PCB layout of this part.

Figure 25. The encoderLCD’s PCB.

### 7.2 PCBs Fabrication and Assembly

Our next step involved the manual fabrication of PCBs for the main board, en-

coderLCD and filter circuits. Following this, we assembled and soldered the elec-

tronic components onto these PCBs. The resulting physical PCBs are illustrated in

Figure 26.

Figure 26. The assembled physical PCBs.

Upon testing these PCBs, we observed a significant improvement in the perfor-

mance of our prototype. The output results demonstrated a marked increase in

precision and accuracy, a clear indication of the benefits of moving from bread-

boards to PCBs. Especially, the values we obtained aligned much more closely with

our calculated theoretical values, providing a strong validation of our design ap-

proach. This confirmed the validity of our previous testing and troubleshooting

stages.

Furthermore, the wanted input values displayed on the LCD interface showed a

high degree of consistency with the actual output results. This correlation be-

tween the displayed and measured values was particularly encouraging, as it con-

firmed the effectiveness of our user interface and the overall system integration.

The improved accuracy and reliability achieved through the use of PCBs repre-

sented a significant milestone in our project's development, bringing us closer to

a finalized, production-ready design. In fact, we placed an order of physical PCBs

for ten devices from a professional manufacturer. This step aimed to validate our

design's reproducibility and enhance the overall reliability and robustness of our

project.

Then, we assembled these PCBs into two metal boxes to make a finished device as

shown below:

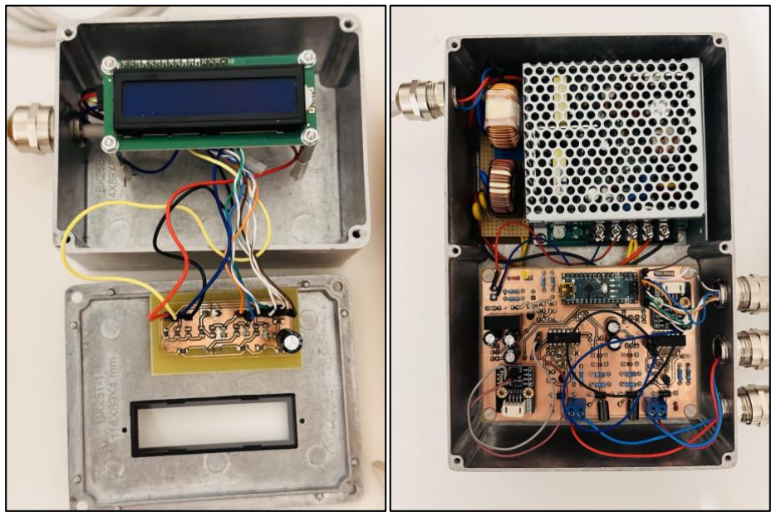
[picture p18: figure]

Figure 27. The finished current loop device.

However, during the development of our finished device, we faced a significant

challenge related to signal integrity, specifically a crosstalk issue arising from the

cable connection between two metal boxes. We used a CAT6 cable to connect the

main board and encoder-LCD circuits, which included four pairs of wires. Initially,

we randomly connected wires to signal pins. Consequently, without adjusting the

encoder, some values on the LCD fluctuated randomly, indicating interference and

noise. To solve this issue, we carefully separated different signals across the avail-

able wire pairs, ensuring that related signals were grouped together within the

twisted pairs. In this device, we assigned dedicated pairs for critical signal combi-

nations such as SDA and SCL for I2C communication, two ground (GND) connec-

tions for proper referencing, encoderA and encoderB for rotary encoder function-

ality, and a pair for the switch signal and 5 V power supply. This approach helped

to minimize the impact of capacitive coupling between different signal types,

thereby preserving the integrity of our data transmission. As a result, the finished

device worked properly.

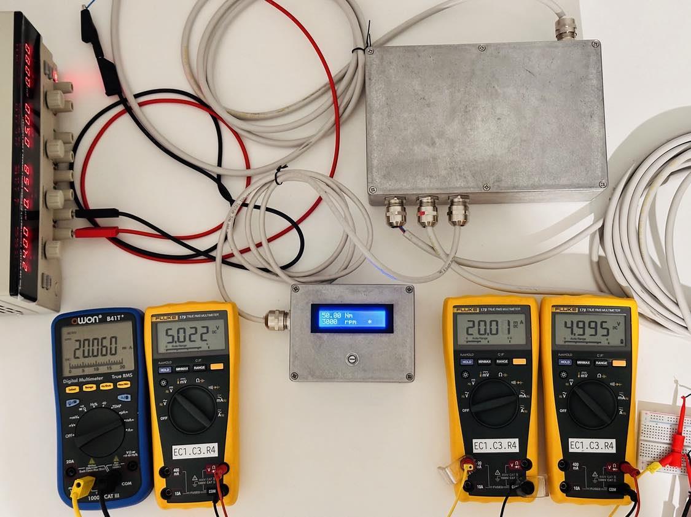
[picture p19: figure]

Figure 28. Testing results of the finished current loop device.

We observed that when the desired torque and speed values were set to 50 Nm

and 3000 rpm respectively, the corresponding current and voltage values meas-

ured approximately 20 mA and 5 V for both channels. These measurements

aligned with the simulation results of the receiver circuit.

### 8 TESTING AND COMPRATIVE ANALYSIS

This chapter describes the output results of ten devices featuring professionally

manufactured PCBs, and compares them to our main prototype.

### 8.1 Testing Finished Current Loop Device with a Real Motor

After the finished current loop device generated stable and accuracy output val-

ues, we started testing it with a real motor by connecting it via a frequency con-

verter. The setup for testing the finished device with the frequency converter is

shown in Figure 29.

Figure 29. Setup for testing the finished device with the frequency converter.

The real-time outputs were also visible in a NCDrive software, as shown in Figure

30 below.

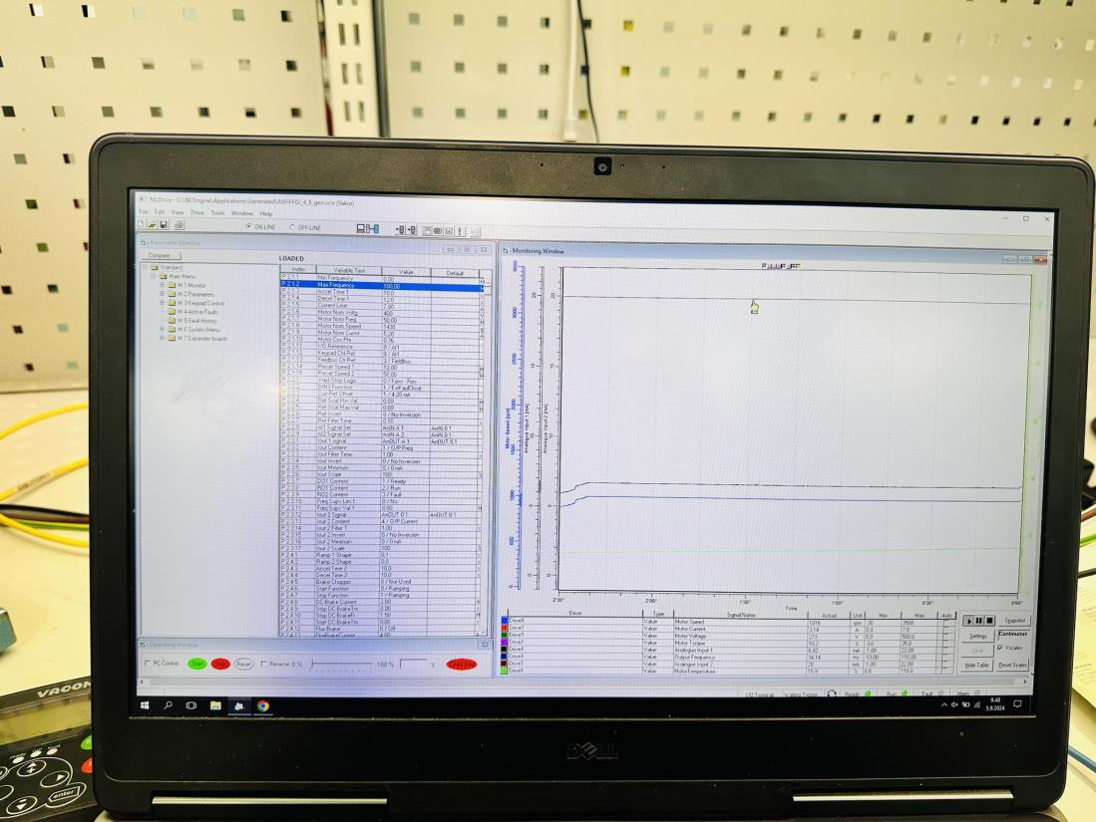
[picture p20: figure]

Figure 30. Real-time outputs displayed in the NCDrive software.

Despite the initial success, we faced challenges with the output stability of the

prototype due to frequency interference. This led to errors or abnormal characters

on the LCD display. Upon investigation, we identified the root causes: unshielded

CAT6 cable and EMC conductors lacking proper grounding. These issues allowed

electromagnetic interference to affect the signal integrity, compromising the reli-

ability of our output results. To eliminate the frequency interference, we imple-

mented EMI shielding tapes around the CAT6 cable and connected all EMC con-

ductors of both metal boxes to the ground. As a result, the device operated with

significantly improved stability.

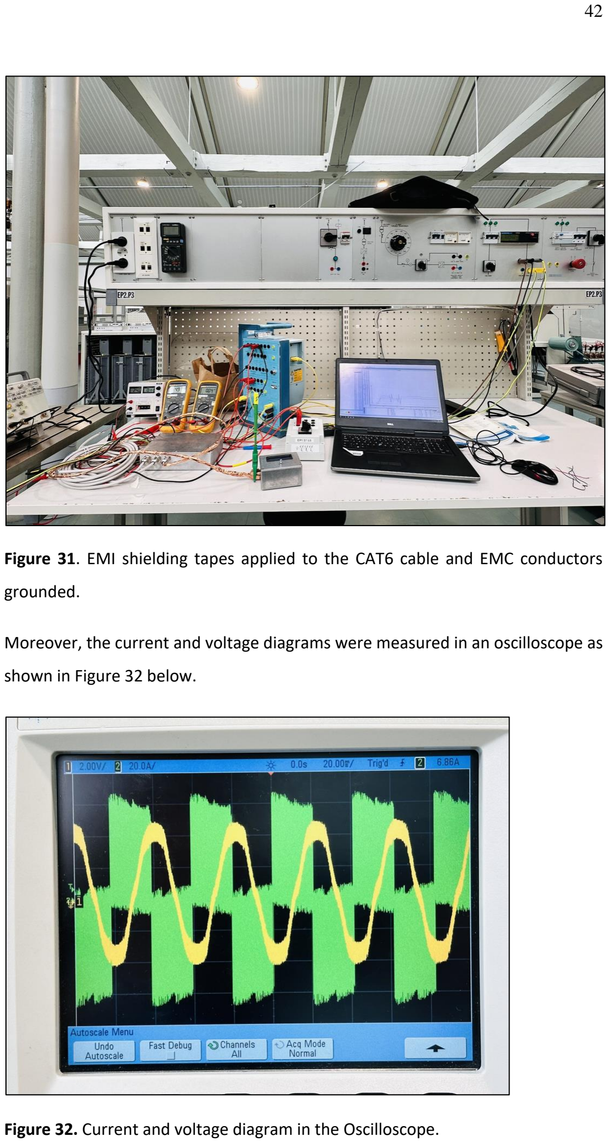
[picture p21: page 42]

Figure 31. EMI shielding tapes applied to the CAT6 cable and EMC conductors

grounded.

Moreover, the current and voltage diagrams were measured in an oscilloscope as

shown in Figure 32 below.

Figure 32. Current and voltage diagram in the Oscilloscope.

### 8.2 Comparative Analysis of Output Results of Ten Devices and Main Prototype

In this project, we used Fluke 179 multimeters to measure output values such as

current. According to the Fluke 179 datasheet (page 11), the accuracy is calculated

using the following formula:

Accuracy = ± ([% of Reading] + [Counts]) = ± (1.0% + 3)

Using this formula, we calculated the total possible measurement error of 0.26 mA

and then converted to an actual current values range of 19.74 mA to 20.26 mA as

shown in Table 3. These calculations provided a framework for interpreting our

results, accounting for equipment limitations when assessing the accuracy and re-

liability of the digital current loop device.

Table 3. Error measurement range for actual current values.

Description | Current value | Unit
Range of currents | 20.00 | mA
Percentage error | 0.20 | mA
Count error | 0.06 | mA
Total possible error | 0.26 | mA
Actual current values | 19.74 mA
| 20.26 mA

We documented torque, speed, and current values for the main prototype across

200 steps, with the full dataset in Appendix 1. Two graphs illustrated our findings:

Figure 33 shows the relationship between desired torque and actual current out-

put, while Figure 34 depicts the desired speed versus real current output.

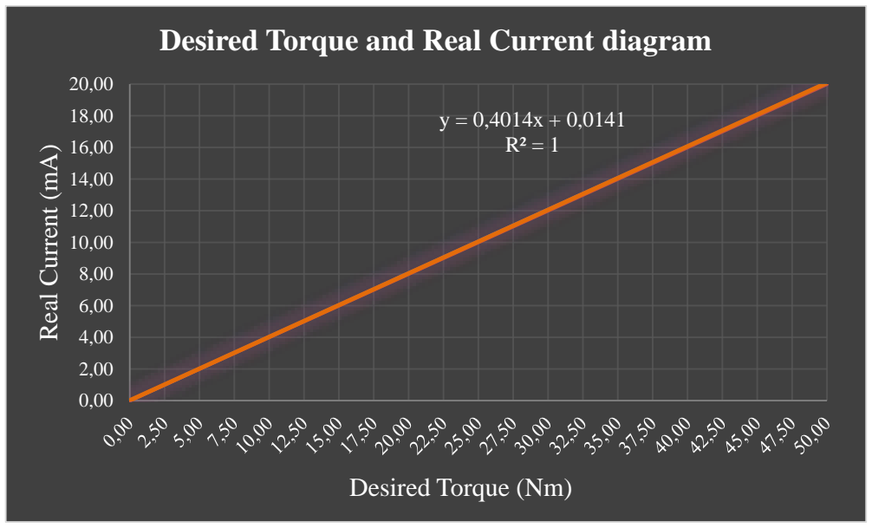
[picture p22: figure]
Real Current (mA); Desired Torque (Nm); Desired Torque and Real Current diagram

Figure 33. Desired torque and real current diagram.

Figure 34. Desired speed and real current diagram.

Additionally, we recorded torque, speed, and current values for ten devices, com-

paring them to the results of the main prototype at 200 steps. The full dataset was

presented in Appendix 2. To illustrate our findings, we created two graphs. Figure

35 shows the relationship between desired torque and actual current output for

all devices, while Figure 36 depicts desired speed versus real current output. These

diagrams were useful to identify performance patterns and deviations among the

manufactured devices.

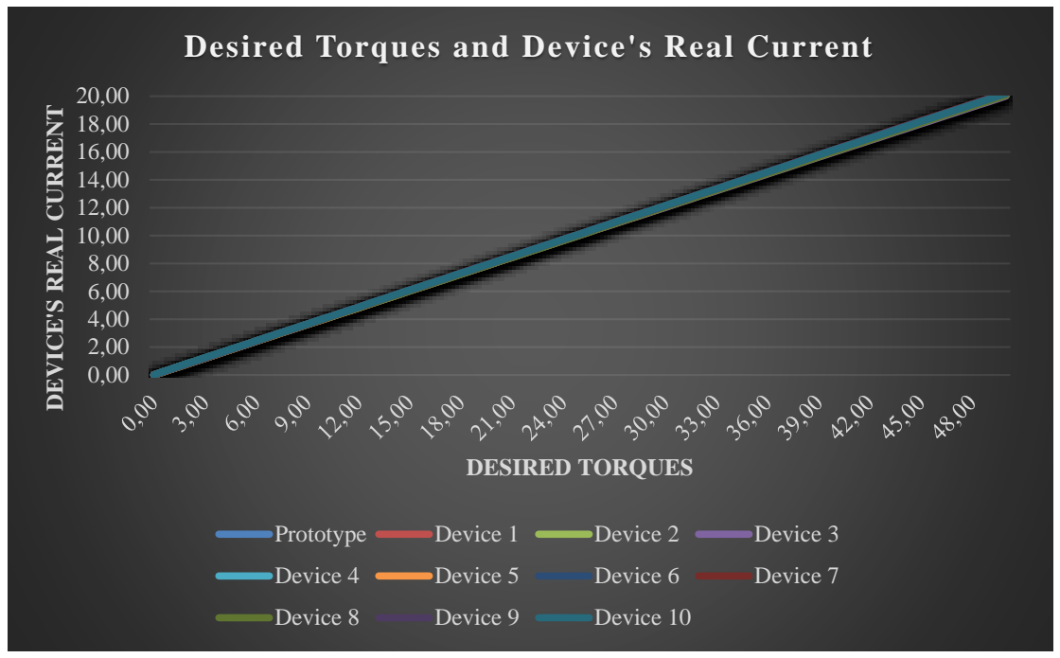
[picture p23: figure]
DEVICE'S REAL CURRENT; DESIRED TORQUES; Prototype; Device 1; Device 2; Device 3; Device 4; Device 5; Device 6; Device 7; Device 8; Device 9; Device 10

Figure 35. Desired torque and actual current output across all devices.

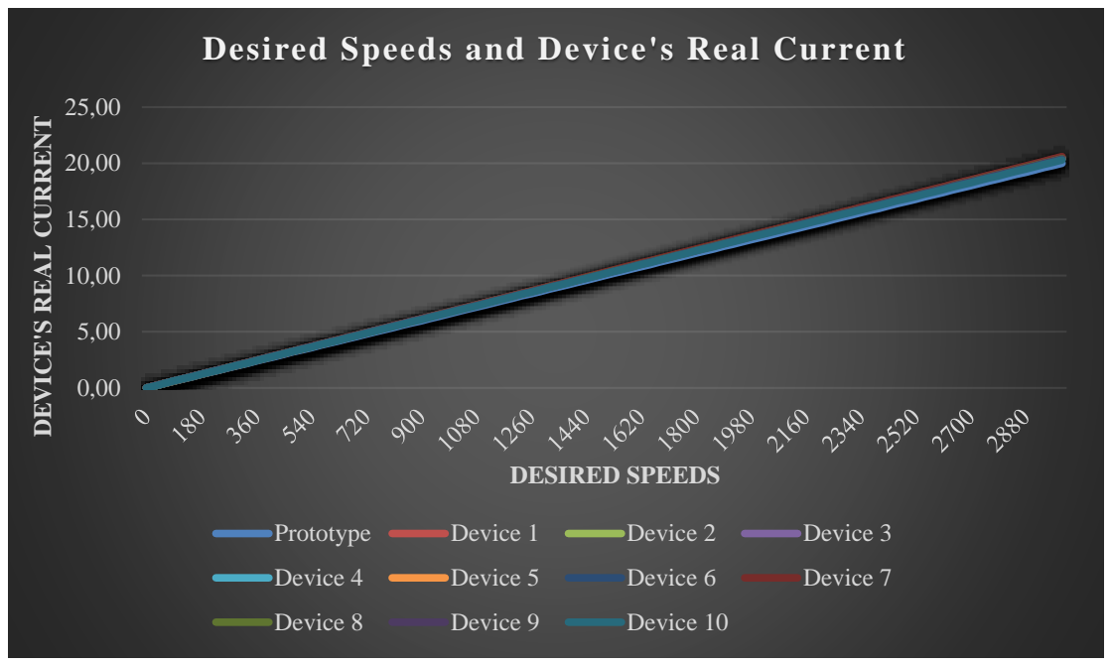
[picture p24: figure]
DEVICE'S REAL CURRENT; DESIRED SPEEDS; Prototype; Device 1; Device 2; Device 3; Device 4; Device 5; Device 6; Device 7; Device 8; Device 9; Device 10

Figure 36. Desired speeds and actual current output across all devices.

As graphs above illustrate, the output torque and speed values of the ten

professionally manufactured devices closely aligned with those of the main

prototype. Minor variations were observed, potentially due to manufacturing

tolerances, component differences, or assembly variations. This close alignment

between the prototype and manufactured units demonstrate a high level of the

robustness and reproducibility of our design.

Desired Torques and Device's Real Current

Desired Speeds and Device's Real Current

### 9 CONCLUSION

The purpose of this project was to design and implement a digital 0 – 20 mA cur-

rent loop device for frequency converters in motor technology applications. The

development process involved three main stages: circuit design, software pro-

gramming, and PCB design and manufacturing. The finished current loop device

can read the desired values input by controlling the rotary encoder and convert

them to analog signal values, creating the 0 – 20 mA current loop transmitting to

Arduino Nano. When connecting this device to both the actual frequency con-

verter and simulated environments using a 250 Ω resistor for testing purposes, we

observed positive relationships between the desired torque (Nm) and speed (rpm)

values and the current values measured by Fluke multimeters. Furthermore, we

noted the same positive correlations with current values for the additional ten de-

vices featuring professionally manufactured PCBs. The following data illustrates

these correlations in detail:

- The desired torque values range from 0 – 50 Nm, with corresponding cur-

rent values measured from 0 – 20 mA.

- The desired speed values range from 0 – 3000 rpm, with corresponding

current values measured from 0 – 20 mA.

The project faced several challenges, including ground noise, poor quality of

breadboards, capacitive cross-talk issue and frequency interference. These were

addressed through the manufacture of integrated PCBs and the implementation

of proper shielding and grounding techniques. The use of CAT6 cables with twisted

pair wiring helped minimize capacitive cross-talk and external interferences. After

eliminating these problems, the finished current loop device worked properly.

In summary, the project successfully achieved its goal of generating a reliable dig-

ital current loop device. However, for further enhancement on the performance

of the device, we would strongly recommend that EMC testing would be imple-

mented on this device. This crucial phase would serve to verify the long-term op-

erational stability of the device and control potential issues that may arise during

extended periods of use. In addition, since the DC power supply converter may generate noise, we also recommend EMC testing on the filter circuit in future de-

velopments. This focused approach would effectively eliminate interference and

noise, further enhancing the accuracy and precision of the device in real-world

applications.

LIST OF REFERENCES

/1/ 1N4148 Datasheet.

/2/ AM2D-2405SZ Datasheet.

/3/ Arduino Nano Datasheet.

/4/ COIL3-100uH Datasheet.

/5/ Datasheet and Manual of I2C LCD1602.

/6/ Datasheet of PEC11R-4220F-S0024 Incremental Encoder.

/7/ DFRobot Gravity 12-Bit I2C DAC Datasheet.

/8/ Dynapar. (n.d.). What is an incremental encoder. https://www.dyna-

par.com/technology/encoder_basics/incremental_en-

coder/#:~:text=What%20is%20an%20Incremental%20Encoder,most%20com-

monly%20used%20rotary%20encoders. (https://www.dynapar.com/technology/encoder_basics/incremental_encoder/)

/9/ Elprocus. (n.d.). About Digital to Analog Converter (DAC) and Its Applications.

https://www.elprocus.com/digital-to-analog-converter-dac-applications/

/10/ Elprocus. (n.d.). What is BC547 Transistor Working and Its Applications.

https://www.elprocus.com/bc547-transistor-working-and-its-applications/

/11/ Filter B82725S2103N003 Datasheet.

/12/ Hoyer. (24 April 2023). Full control and optimised operation with frequency

converters. https://hoyermotors.com/about-hoyer/information/product-and-

market-news/full-control-and-optimised-operation-with-frequency-converters/ (https://hoyermotors.com/about-hoyer/information/product-and-market-news/full-control-and-optimised-operation-with-frequency-converters/)

/13/ LM324 Datasheet.

/14/ Mauricio, D. (n.d.). Why a 0 mA Signal is Not Practical.

https://www.predig.com/whitepaper/why-0-ma-signal-not-practical

/15/ Paonessa, S. (n.d.). Ground loops & Non-Isolated Commons.

https://www.predig.com/indicatorpage/ground-loops-non-isolated-commons

/16/ Paonessa, S. and McDuffee, B. (n.d.). Back to Basics: The Fundamentals of 4

– 20 mA Current Loops. https://www.predig.com/indicatorpage/back-basics-fun-

damentals-4-20-ma-current-loops (https://www.predig.com/indicatorpage/back-basics-fundamentals-4-20-ma-current-loops)

/17/ Souza, R. (n.d.) I2C Protocol. https://www.prodigytechno.com/i2c-protocol

/18/ Specification for Approval of Coil3.

/19/ TL431 Datasheet.

/20/ Toroidal Inductor (Vertical, 100uH) Datasheet.

/21/ TR5-K Datasheet.

/22/ TVS Diodes Datasheet (P6KE Series).

/23/ TVS Varistor Datasheet.

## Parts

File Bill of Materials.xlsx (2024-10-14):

 |  | Bill of Materials |  |  |  |  | Note
Supplier | No. | Description | Order Code | Quantity | Unit Price (incl. VAT) (EUR) | Price (incl. VAT) (EUR) | Reference | Supplier
Elfa | 1 | Capacitor 100NF_50V_CER | 165-77-688 | 23 | 0.37 | 8.62 | C1-C6, C8, C10-C13, C15, C17, C19-C26,C6, C8, C10, C12 | https://www.elfadistrelec.fi/fi/keraaminen-kondensaattori-100nf-50vdc-1206-10-kemet-c1206c104k5rac7025/p/16577688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
Elfa | 2 | Capacitor 100UF_50V_ELE | 300-92-030 | 7 | 0.19 | 1.31 | C7, C9, C14, C16, C18, C3, C27 | https://www.elfadistrelec.fi/fi/radiaalinen-elektrolyyttikondensaattori-100uf-50ua-50v-200ma-rnd-rnd-150ehr101m50b/p/30092030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
Elfa | 3 | ROW_VERT_1X8 | 43-70-219 | 1 | 1.18 | 1.18 | ROW_VERT/1X1, ROW_VERT/1X2 | https://www.elfadistrelec.fi/fi/piikkirima-uros-1a-kontaktien-maeaerae-36-prostar-ss-1x36-t1-3mm/p/14370219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
Elfa | 4 | LCD holder for the small metal box | 175-57-723 | 1 | 21.06 | 21.06 | LCD holder for the small metal box | https://www.elfadistrelec.fi/fi/lcd-naeytoen-etukehys-display-visions-ea-017-2uke/p/17557723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
Elfa | 5 | Cable CAT6 1.5m | 302-29-454 | 1 | 5.99 | 5.99 | Cable CAT 6 1.5m | https://www.elfadistrelec.fi/fi/kytkentaekaapeli-rj45-urosliitin-rj45-urosliitin-cat-ftp-5m-harmaa-rnd-rnd-765-00207/p/30229454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
Elfa | 6 | EMC sleeve seal | 301-40-348 | 5 | 8.71 | 43.55 | EMC sleeve seal | https://www.elfadistrelec.fi/fi/emc-holkkitiiviste-10mm-m16-wiska-ltd-10065017/p/30140348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
Farnell | 7 | GreenLED | 3796272 | 1 | 0.28 | 0.28 | Green1 | https://fi.farnell.com/en-FI/multicomp-pro/mp008246/led-green-1-5mcd-572nm-3mm/dp/3796272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
Farnell | 8 | Arduino_Nano_v3.x | 1848691 | 1 | 26.08 | 26.08 | A1 | https://fi.farnell.com/arduino/a000005/arduino-nano-evaluation-board/dp/1848691
Farnell | 9 | BC547_TO92_0.1A | 1017673 | 2 | 0.15 | 0.31 | BC547_1, BC547_2 | https://fi.farnell.com/en-FI/onsemi/bc547bg/transistor-npn-45v-0-1a-to92/dp/4182292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
Farnell | 10 | 1N4148 | 9843680 | 4 | 0.02 | 0.08 | D2-D5 | https://fi.farnell.com/en-FI/multicomp-pro/1n4148/diode-ultrafast-recovery-150ma/dp/2306362?st=1N4148
Farnell | 11 | P6KE43CA/P6KEG39CA | 3226355 | 5 | 0.34 | 1.68 | D6-D13,D1 | https://fi.farnell.com/en-FI/multicomp-pro/p6keg39ca/tvs-diode-600w-33-3v-bidir-do/dp/3226355
Farnell | 12 | Resistor 1.8k SMD (replace by 2 TH resistors of 910R) | Removed |  |  | 0.00 |  | https://fi.farnell.com/en-FI/panasonic/era8aeb182v/res-1k8-0-1-0-25w-1206-metal-film/dp/1841759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
Farnell | 13 | Resistor 10k SMD (update footprint from 2010 to 1206) | 1469655 | 12 | 0.42 | 5.06 | R2, R3, R5, R6, R1-R8 | https://fi.farnell.com/en-FI/vishay/crcw120610k0jnea/res-10k-5-0-25w-1206-thick-film/dp/1469655
Farnell | 14 | Resistor 470R SMD (update footprint from 0805 to 1206) | 2671182 | 1 | 0.02 | 0.02 | R4 | https://fi.farnell.com/en-FI/walsin/wr12x471-jtl/res-470r-5-0-25w-1206-thick-film/dp/2671182
Farnell | 15 | Resistor 150k SMD | 1841797 | 8 | 0.36 | 2.90 | R7, R8, R11, R12, R15-R18 | https://fi.farnell.com/en-FI/panasonic/era8aeb154v/res-150k-0-1-0-25w-1206-metal/dp/1841797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
Farnell | 16 | Resistor 100R SMD | 3392888 | 2 | 0.05 | 0.10 | R19, R20 | https://fi.farnell.com/en-FI/multicomp-pro/mp003694/res-100r-1-0-25w-1206-thick-film/dp/3392888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
Farnell | 17 | Resistor 100R TH (change from 400mW to 600mW) | 9463909 | 4 | 0.18 | 0.72 | R9, R13, R21, R23 | https://fi.farnell.com/vishay/mrs25000c1000fct00/res-100r-1-600mw-axial-metal-film/dp/9463909
Farnell | 18 | Resistor 150R TH (change from 250mW to 600mW) | 9464638 | 4 | 0.18 | 0.71 | R10, R14, R22, R24 | https://fi.farnell.com/vishay/mrs25000c1500fct00/res-150r-1-600mw-axial-metal-film/dp/9464638
Farnell | 19 | Resistor 2.2k TH (change from 2W to 600mW) | 9466711 | 2 | 0.18 | 0.36 | R25, R26 | https://fi.farnell.com/vishay/mrs25000c2201fct00/res-2k2-1-600mw-axial-metal-film/dp/9466711
Farnell | 20 | SOCKET_1X8 (replace for ROW_VERTICAL HEADER at mainboard) | 2802333 | 1 | 1.08 | 1.08 | Replace for ROW_VERTICAL PIN HEADER at mainboard | https://fi.farnell.com/en-FI/mcm/83-15410/1-x-8-position-female-socket-with/dp/2802333?MER=sy-me-pd-mi-acce
Farnell | 21 | SOCKET*2_1X10 | 1593464 | 1 | 0.53 | 0.53 | SOCKET/1X1, SOCKET/1X2 | https://fi.farnell.com/multicomp/2212s-10sg-85/socket-pcb-1-row-10way/dp/1593464?MER=sy-me-pd-mi-alte
Farnell | 22 | TL431CLP_TO92 | 9756450 | 1 | 0.88 | 0.88 | TL431CLP1 | https://fi.farnell.com/stmicroelectronics/tl431acz/voltage-ref-shunt-2-495v-36v-to/dp/9756450
Farnell | 23 | TM_BLOCK_2P | 3882652 | 4 | 2.36 | 9.42 | TM_BLOCK/2P1-TM_BLOCK/2P3 | https://fi.farnell.com/camdenboss/ctb0308-2/terminal-block-wire-to-brd-2pos/dp/3882652
Farnell | 24 | DFR0552 | 3517945 | 2 | 6.22 | 12.45 | U1, U2 | https://fi.farnell.com/dfrobot/dfr0552/i2c-12-bit-dac-module-arduino/dp/3517945
Farnell | 25 | Capacitor 10NF_50V_CER SMD (update footprint from 0402 to 1206) | 2906003 | 3 | 0.13 | 0.40 | C1, C2, C4 | https://fi.farnell.com/kemet/c0402c103j5racauto/cap-0-01-f-50v-5-x7r-0402/dp/2904528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
Farnell | 26 | ROW_VERT_1X4 | 2852586 | 1 | 0.27 | 0.27 | ROW_VERT/1X1 | https://fi.farnell.com/en-FI/multicomp/mc-hvt1-s04-g/connector-header-4pos-1row-1-27mm/dp/2852586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
Farnell | 27 | TVS Varistor | 1004301 | 1 | 1.12 | 1.12 | RV1 | https://fi.farnell.com/epcos/b72220s0500k101/varistor-27-0j-50vac/dp/1004301
Farnell | 28 | Filter B82725S2103N003 | 3580935 | 1 | 11.21 | 11.21 | FL1 | https://fi.farnell.com/epcos/b82725s2103n003/power-line-choke-ring-core-2-8mh/dp/3580935
Farnell | 29 | Toroidal Inductor, Vertical, 100uH | 2215971 | 1 | 6.65 | 6.65 | L1 | https://fi.farnell.com/pulse-electronics/pe-92112knl/inductor-100uh-smt-5a-35-6x35/dp/2215971
Farnell | 30 | Capacitor 10nF TH | 2576736 | 1 | 0.35 | 0.35 | C2 (filter circuit) | https://fi.farnell.com/walsin/yv1ac103m140d20c7b/cap-0-01-f-20/dp/2576736
Farnell | 31 | Capacitor 2200pF TH | 2507755 | 2 | 0.60 | 1.19 | C1 and C3 (filter circuit) | https://fi.farnell.com/vishay/vy1222m47y5uq6uv0/cap-2200pf-20/dp/2507755
Farnell | 32 | Encoder's knob | Removed |  |  | 0.00 | Encoder's knob | https://fi.farnell.com/alcoswitch-te-connectivity/pka50b1-4/ribbed-knob-black-20-2mm/dp/3133342
Farnell | 33 | Screw 3.5x12mm | 2400762 | 12 | 2.32 | 27.83 | Screw 3.5x12mm | https://fi.farnell.com/deltron-components/000-035-004/std-screw-m3-5-stainless-steel/dp/2400762
Farnell | 34 | Heat Sink, 60 °C/W, TO-92, 15.29 mm, 18.29 mm | 2822615 | 2 | 6.26 | 12.52 | Heatsink for TO-92 transistor | https://fi.farnell.com/en-FI/aavid-thermalloy/575200b00000g/heat-sink-aluminium/dp/2822615
Farnell | 35 | Resistor 910R TH | 9470581 | 2 | 0.17 | 0.35 | R1, R29 | https://fi.farnell.com/en-FI/vishay/mrs25000c9100fct00/res-910r-1-600mw-axial-metal-film/dp/9470581
Farnell | 36 | Resistor 0R SMD | 9240276 | 1 | 0.04 | 0.04 | R27 | https://fi.farnell.com/en-FI/yageo/rc1206jr-070rl/res-0r0-5-0-25w-1206-thick-film/dp/9240276
Farnell | 37 | Resistor 150R SMD | 2531869 | 1 | 0.24 | 0.24 | R28 | https://fi.farnell.com/en-FI/te-connectivity/crgs1206j150r/res-150r-5-1206-thick-film/dp/2531869
Farnell | 38 | TM_BLOCK_3P | 3882664 | 1 | 3.45 | 3.45 | TM_BLOCK_3P (filter circuit) | https://fi.farnell.com/camdenboss/ctb0308-3/terminal-block-wire-to-brd-3pos/dp/3882664?cfm=true
Partco | 39 | LCD I2C | LCD 2X16-I2C | 1 | 12.80 | 12.80 | LCD I2C | https://www.partco.fi/fi/naeytoet/lcd-naeytoet/20158-lcd-2x16-i2c.html
Partco | 40 | Heatsinks for power chip (2pcs/1bag) | RPI-02893 | 1 | 4.80 | 4.80 | Heatsinks for power chip | https://www.partco.fi/fi/laemmoenhallinta/jaeaehdytyselementit/26948-rpi-02893.html
Starelec | 41 | TR5-K | 170-00181 | 1 | 0.55 | 0.55 | F1 | https://www.starelec.fi/product_info.php?cPath=66_335_3295&products_id=25786
Starelec | 42 | COIL3-100UH (mainboard) | COIL3-100UH | 4 | 0.50 | 2.00 | L1-L4 | https://www.starelec.fi/product_info.php?products_id=21043
Starelec | 43 | AM2D-2405SZ | DC2WS-2405S | 1 | 7.06 | 7.06 | PS1 | https://www.starelec.fi/product_info.php?cPath=72_155_2374&products_id=16073
Starelec | 44 | LM324NE4 | LM324N | 2 | 0.74 | 1.48 | U3, U4 | https://www.starelec.fi/product_info.php?products_id=112
Starelec | 45 | Incremental Encoder PEC11R-24-4215K | PEC11R-24-4215K | 1 | 3.26 | 3.26 | SW1 | https://www.starelec.fi/product_info.php?products_id=28035
Starelec | 46 | Metal box 222.1x145.9x55.9mm (BS11) | 459GP | 1 | 28.25 | 28.25 | Metal box 222.1x145.9x55.9mm (BS11) | https://www.starelec.fi/product_info.php?cPath=81_862_863&products_id=10199
Starelec | 47 | Metal box 114.7x89.7x55.1mm (455-00705) | 459CP | 1 | 9.10 | 9.10 | Metal box 114.7x89.7x55.1mm (455-00705) | https://www.starelec.fi/product_info.php?cPath=81_862_863&products_id=10196
Starelec | 48 | Isolation DC/DC converter 24V/24V DC | SD-25B-24 | 1 | 36.70 | 36.70 | Isolation DC/DC converter 24V/24V DC | https://www.starelec.fi/product_info.php?cPath=72_155_2871&products_id=19831
Starelec | 49 | Connectors for wires connected to row_vertical pin | WJW-MF-100 | 1 | 3.21 | 3.21 | Female/Male jumper wires | https://www.starelec.fi/advanced_search_result.php?keywords=WJW-MF-100&x=18&y=17
Starelec | 50 | Female/Female jumer wires for the connection btw LCD and small pcb | WJW-FF-200 | 1 | 4.28 | 4.28 | Female/Female jumer wires for the connection btw LCD and small pcb | https://www.starelec.fi/product_info.php?products_id=35043
Starelec | 51 | Cable for power supply and 2 current loops (3x2m about) | LIYCY2X0.5 | 6 | 1.81 | 10.86 | Cable for power supply and 2 current loops | https://www.starelec.fi/advanced_search_result.php?keywords=LIYCY2X0.5&x=14&y=7
Starelec | 52 | Laitenuppi muovi 6mm/16mm harmaa/musta | GMN6G-MU | 1 | 0.78 | 0.78 | Encoder's knob | https://www.starelec.fi/product_info.php?products_id=16188
 | Total price |  |  |  |  | 335.09
 | *Note: The unit prices were included VAT

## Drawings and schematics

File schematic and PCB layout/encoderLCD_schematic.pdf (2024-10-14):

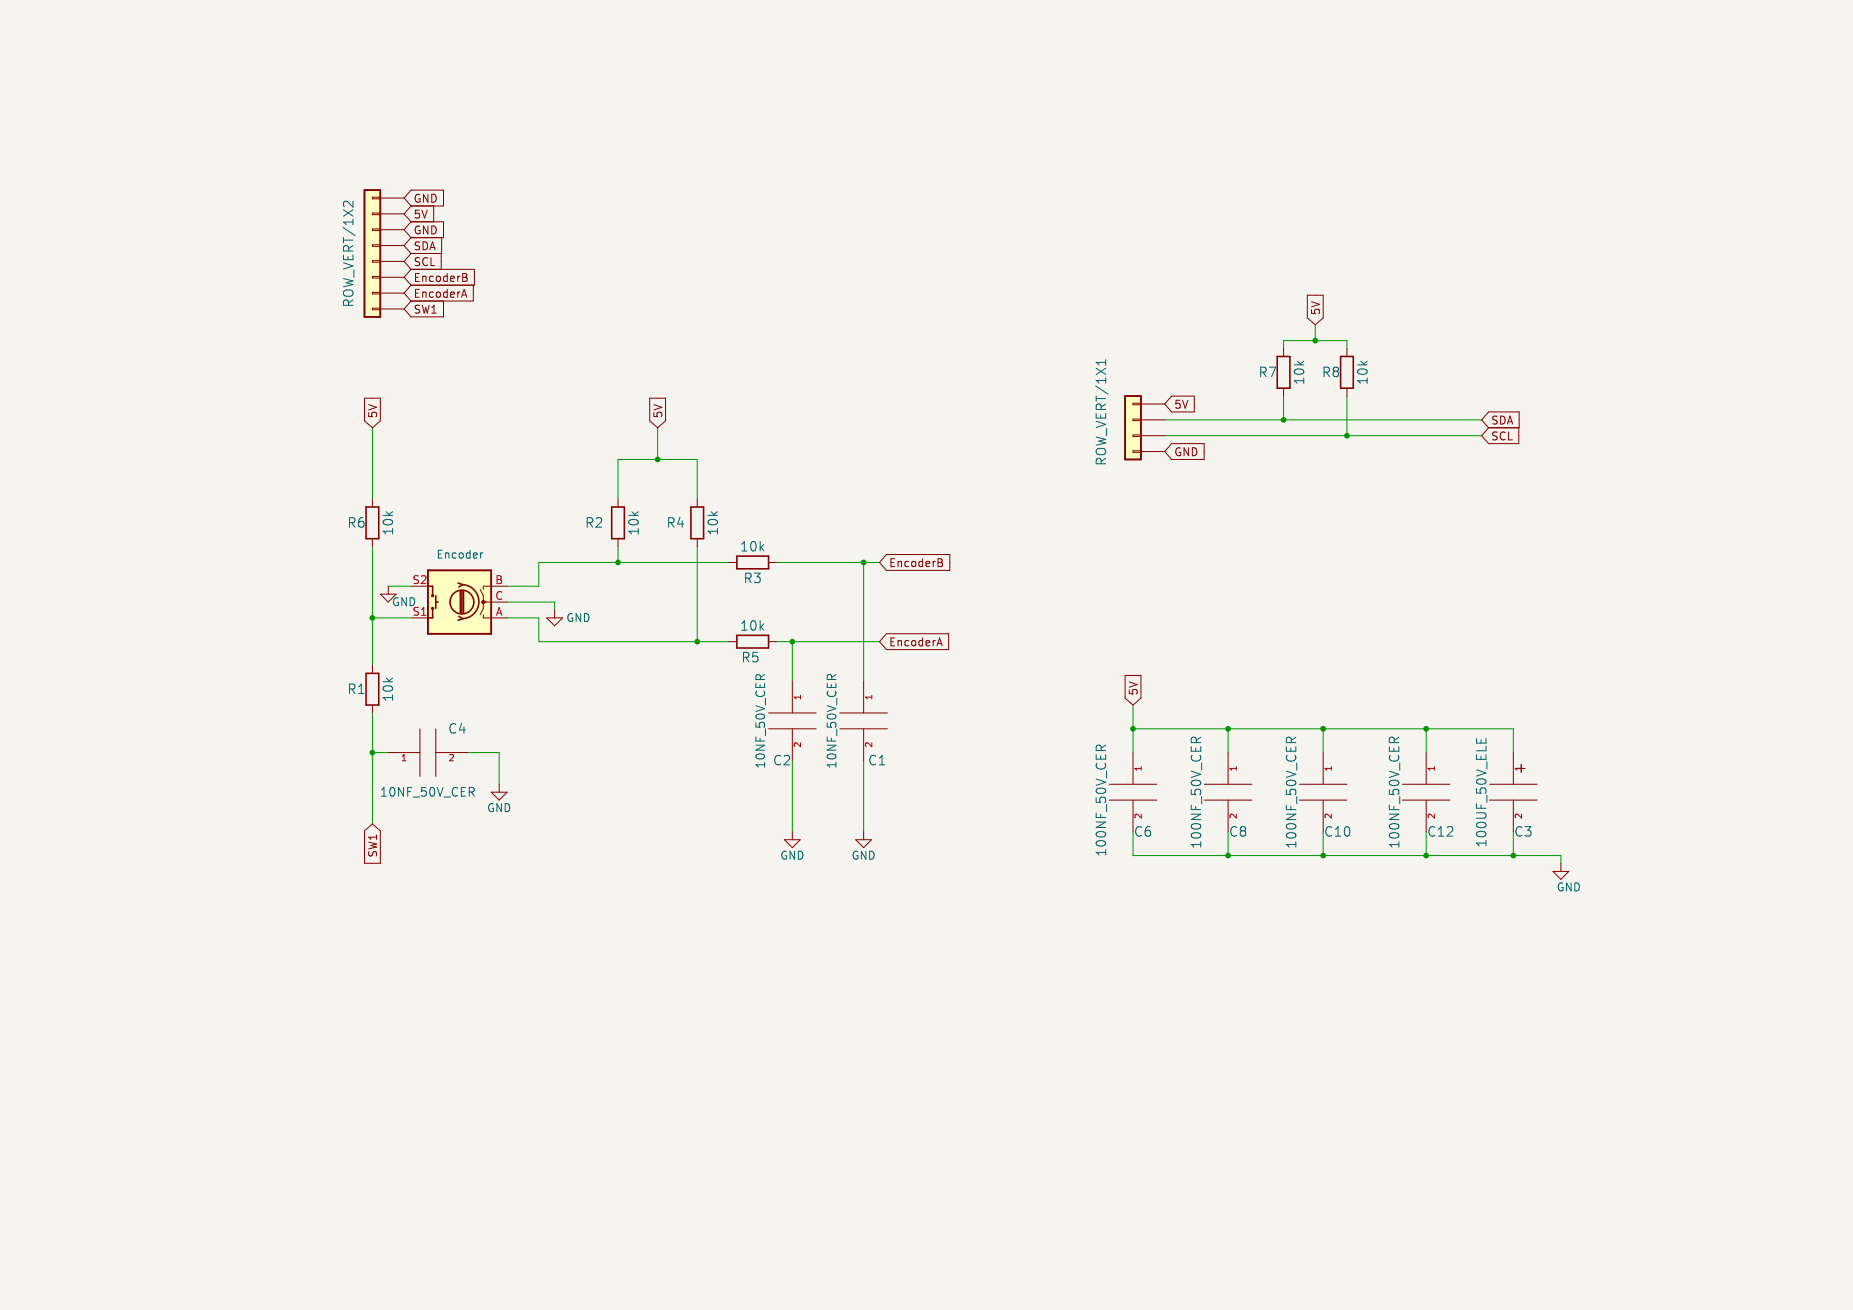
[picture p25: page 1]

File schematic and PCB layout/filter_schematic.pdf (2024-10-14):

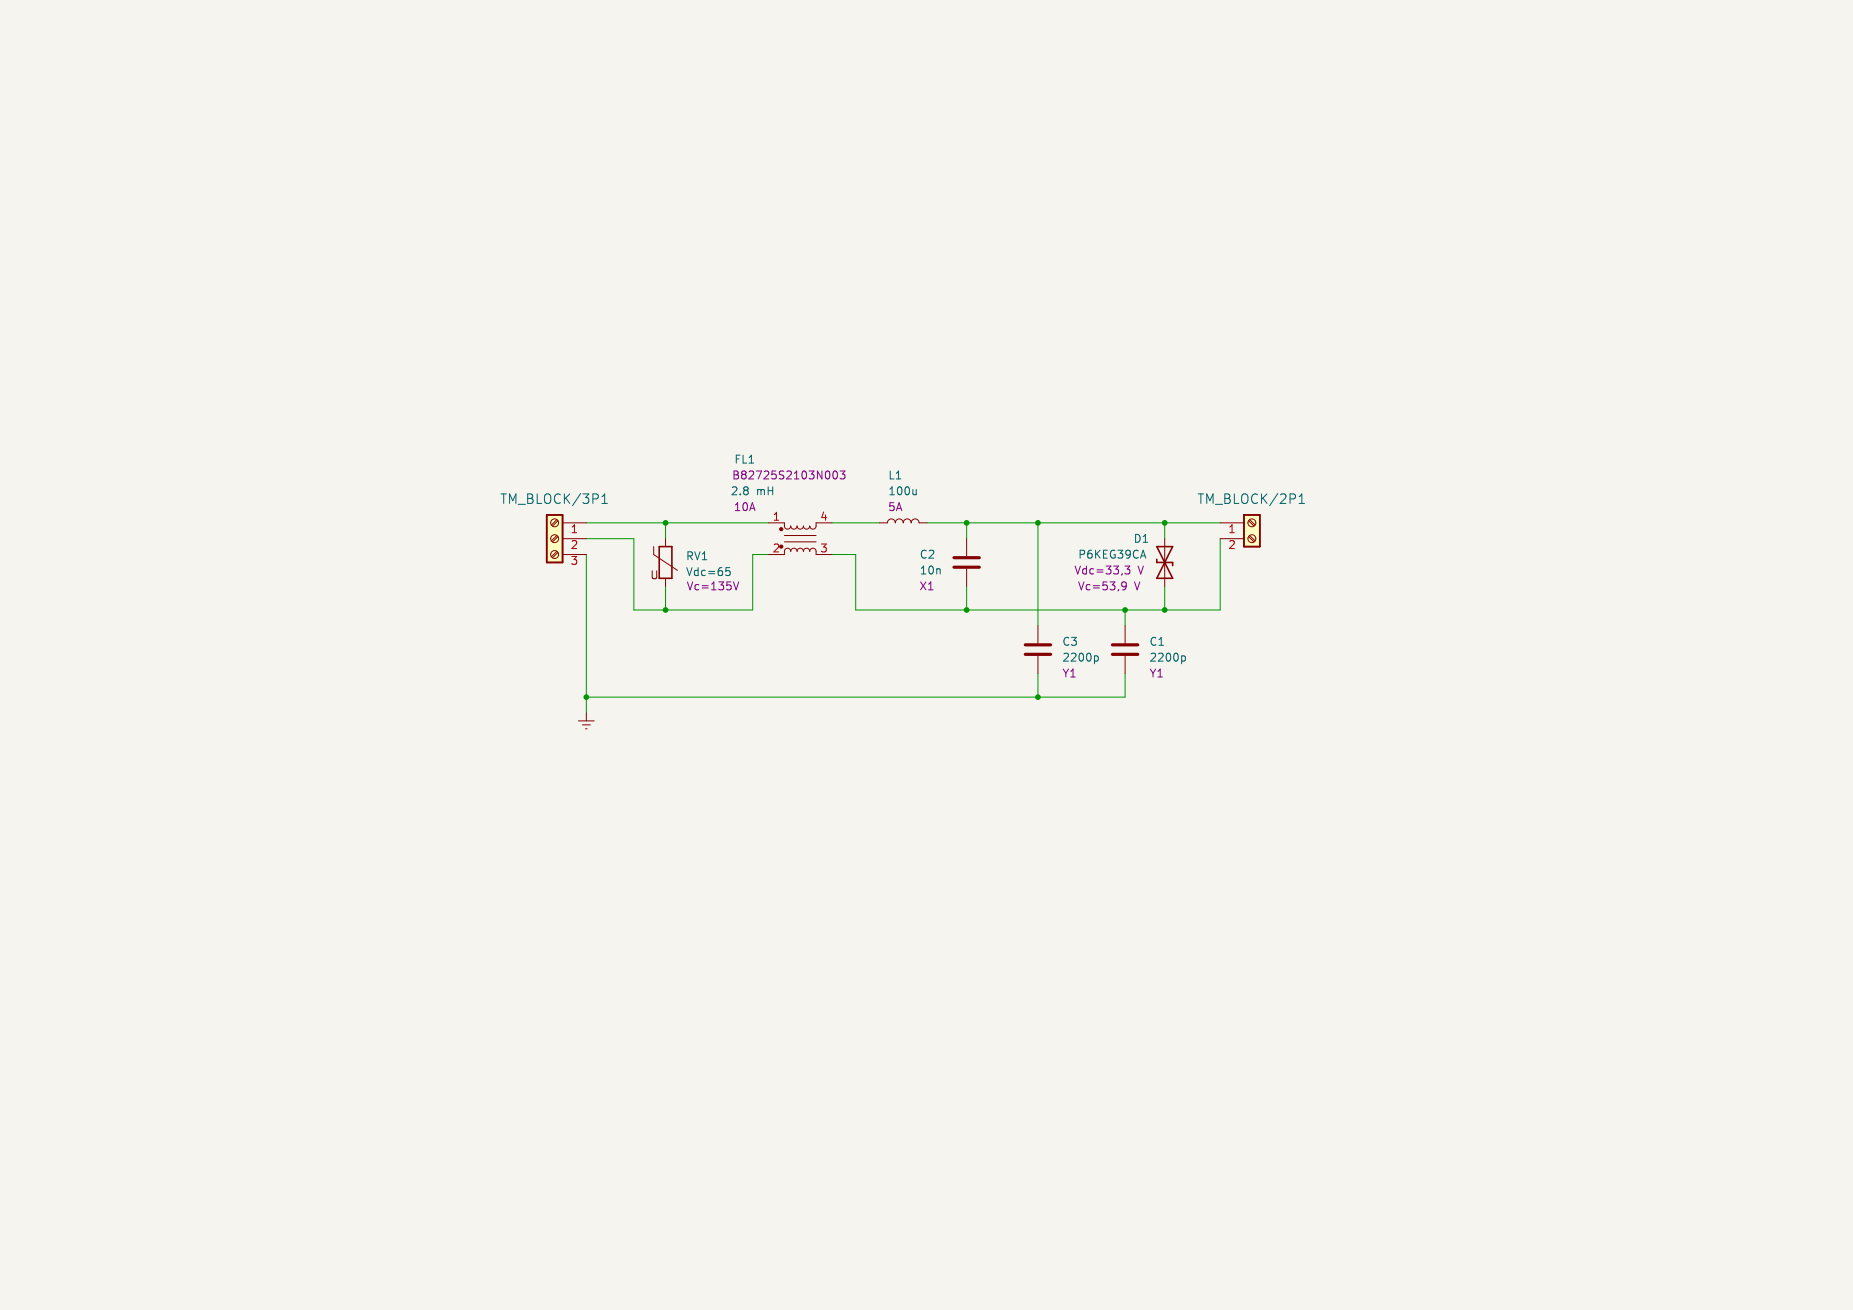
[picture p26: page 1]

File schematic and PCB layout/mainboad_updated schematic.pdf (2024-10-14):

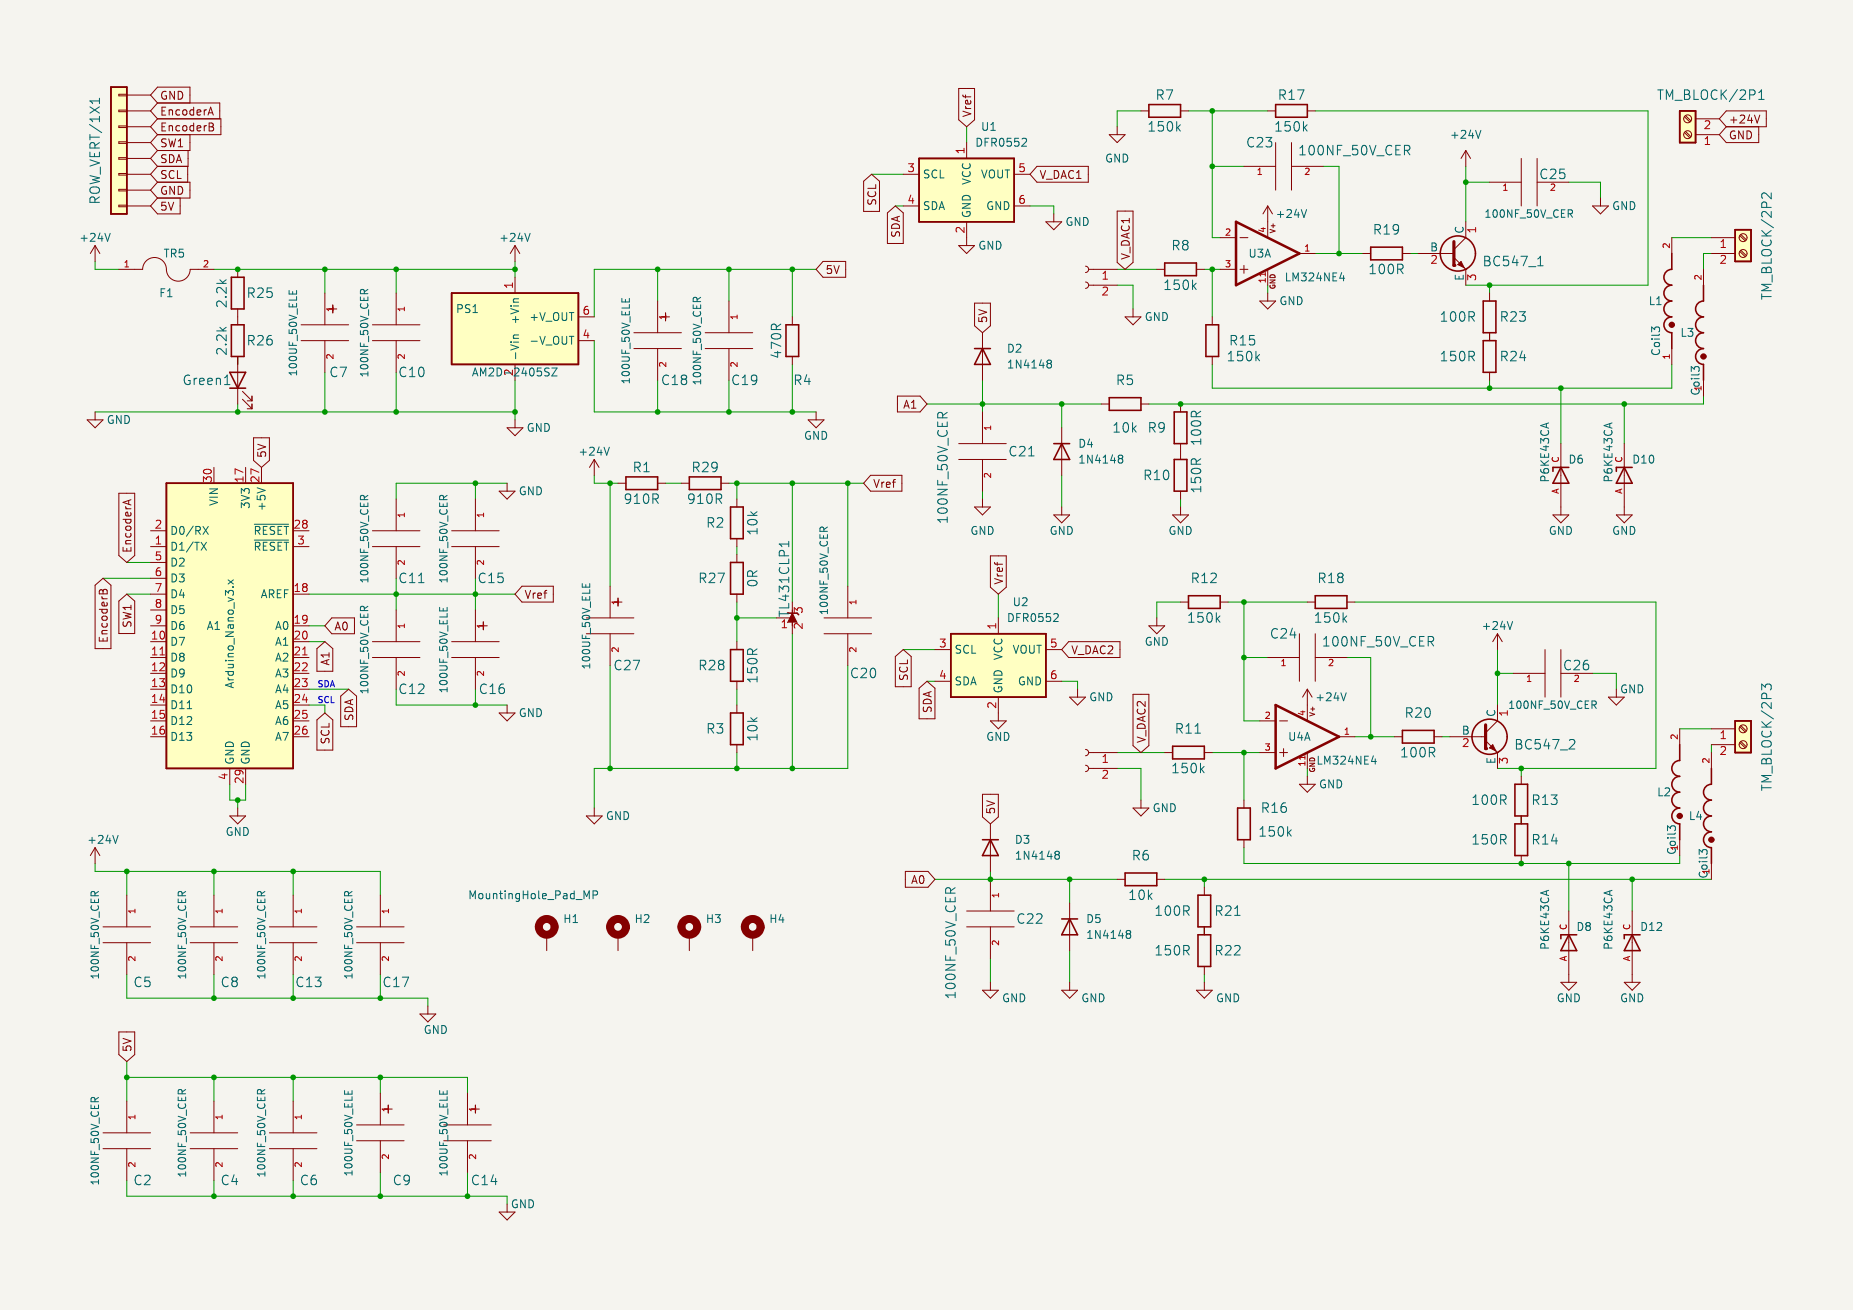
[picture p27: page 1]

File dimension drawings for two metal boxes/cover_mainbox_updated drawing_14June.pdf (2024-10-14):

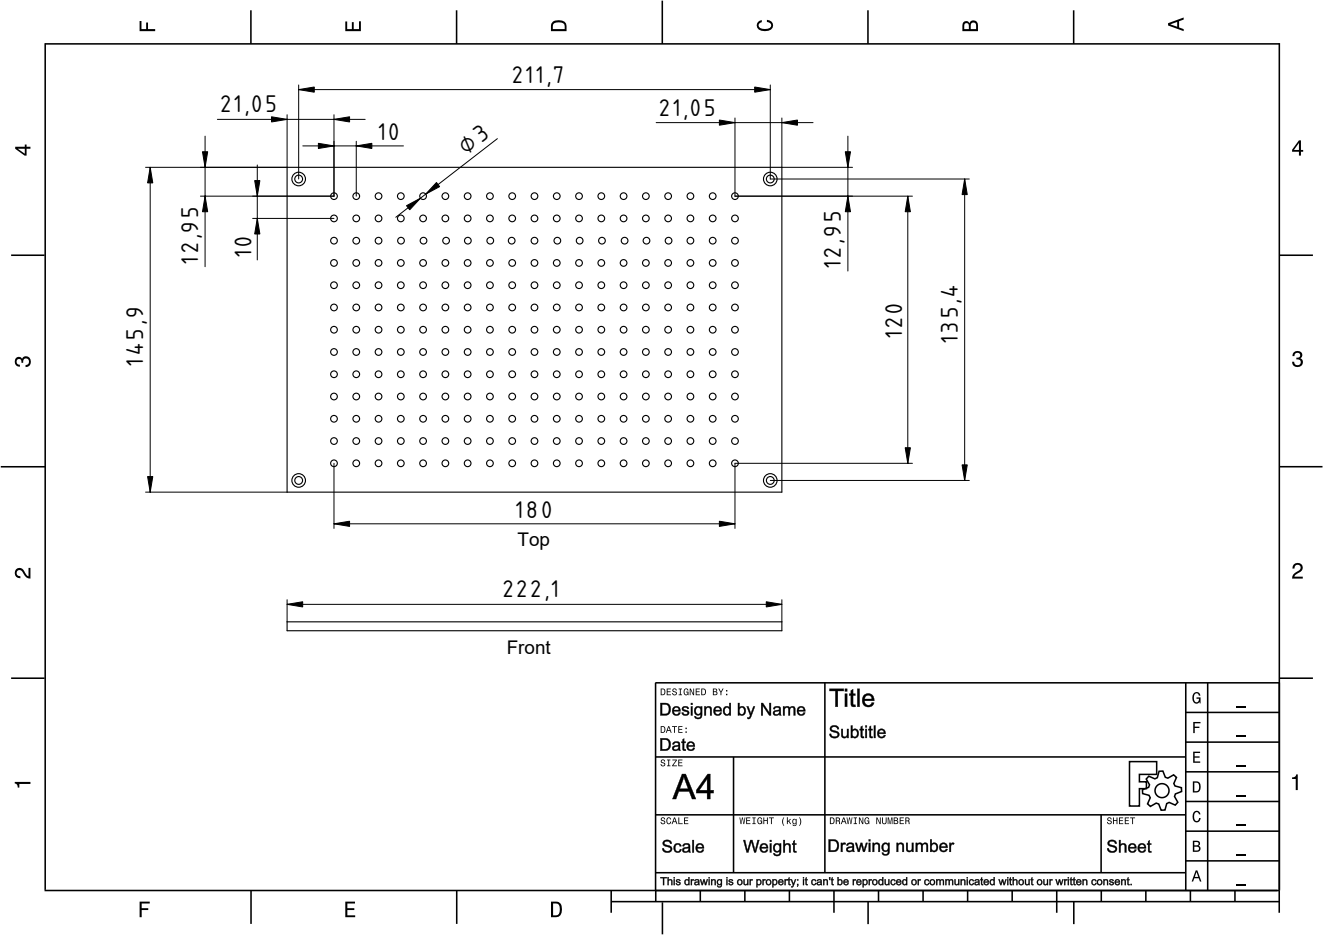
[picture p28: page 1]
Front; Top

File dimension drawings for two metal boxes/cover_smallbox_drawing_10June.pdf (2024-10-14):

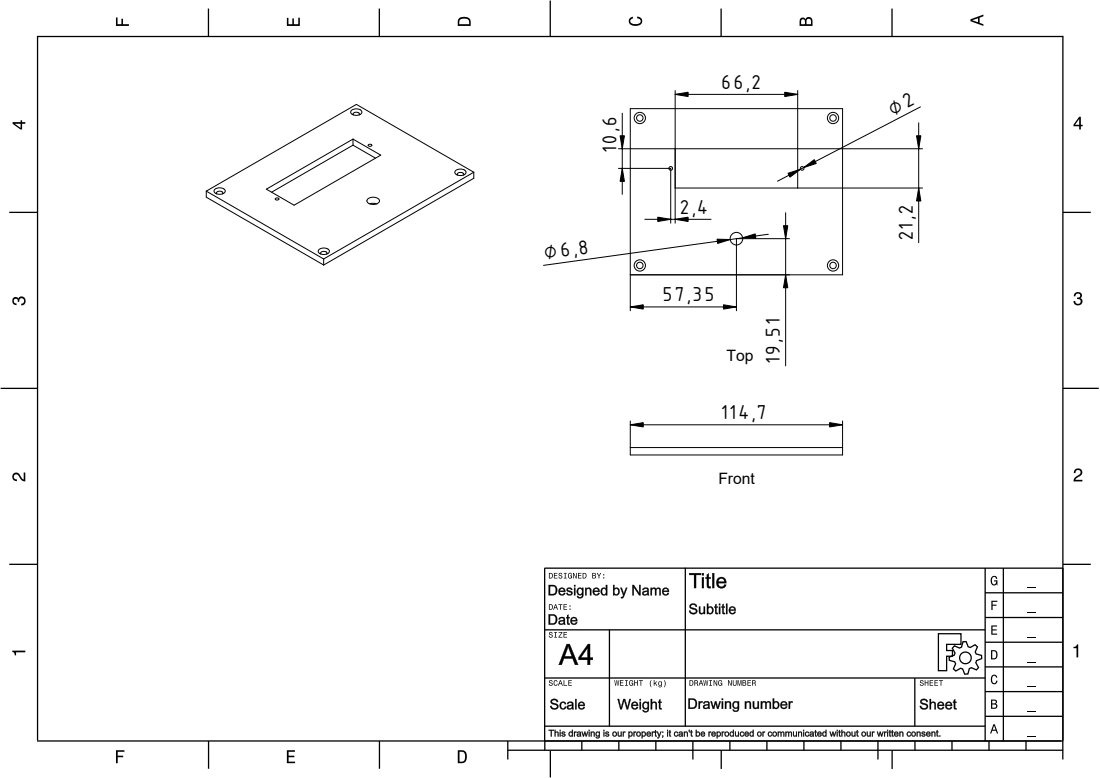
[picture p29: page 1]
Front; Top

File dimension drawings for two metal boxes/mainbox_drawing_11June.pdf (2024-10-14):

13,41 ⌀3,5⌀3,5

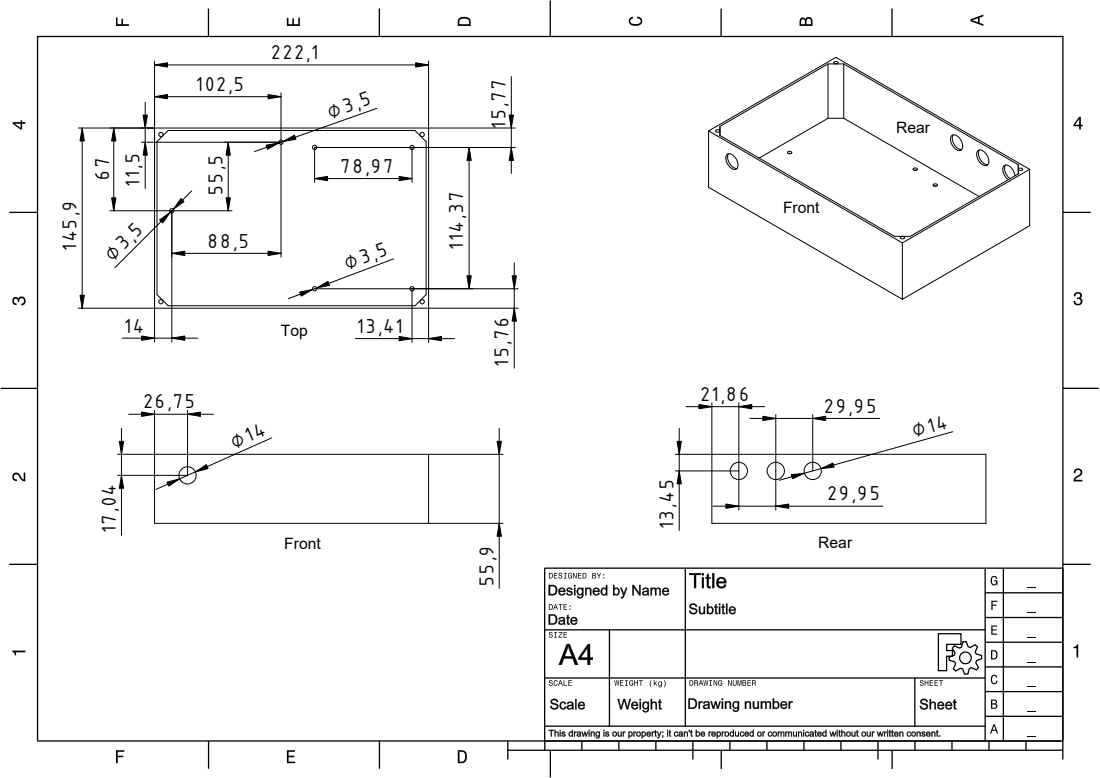
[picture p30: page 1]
Top; Rear; Front

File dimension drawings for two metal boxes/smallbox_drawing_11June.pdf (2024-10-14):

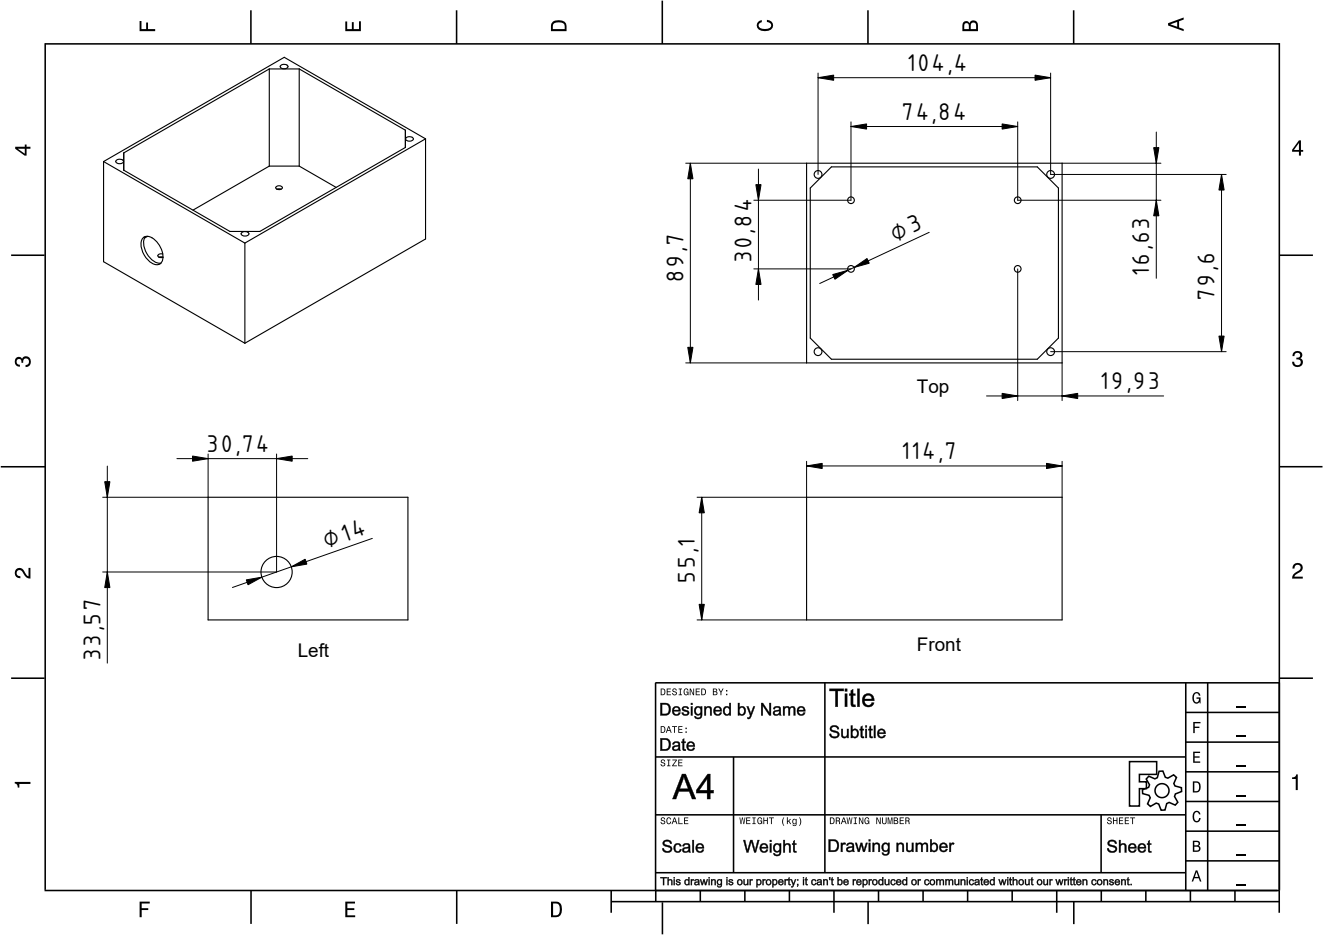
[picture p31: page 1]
Left; Front; Top

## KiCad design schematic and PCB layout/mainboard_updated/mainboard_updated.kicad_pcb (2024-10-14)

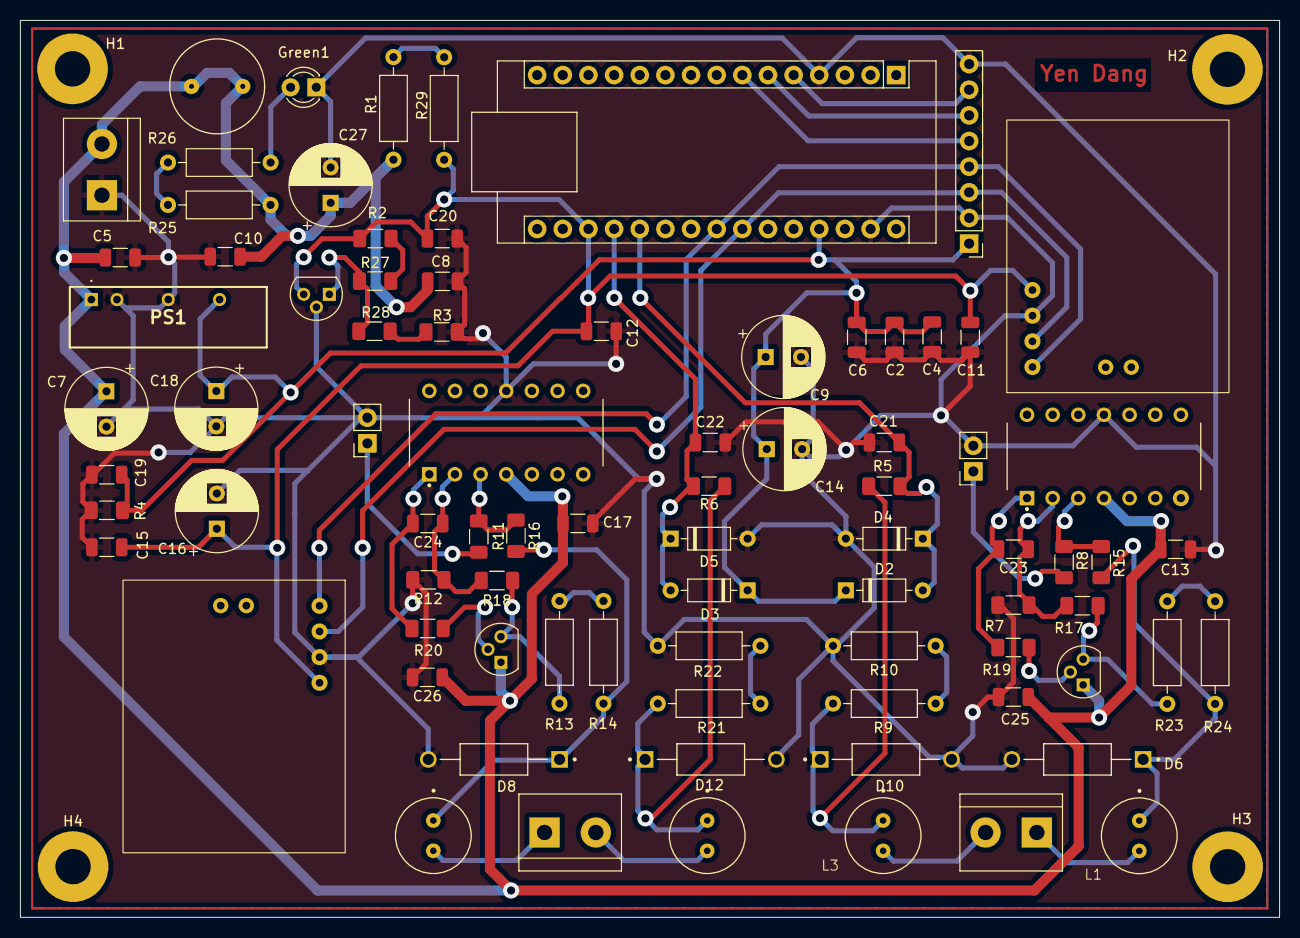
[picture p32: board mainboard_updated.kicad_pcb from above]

Board: 2 copper layers, 124.7 x 88.8 mm, 87 parts (0 on the bottom side), 41 nets.

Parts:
 Green1: GreenLED; LED
A1: Arduino_Nano_v3.x; Arduino_Nano
BC547_1, BC547_2: BC547_TO92_0.1A; TO-92
C2, C4, C5, C6, C8, C10, C11, C12, C13, C15, C17, C19, C20, C21, C22, C23, C24, C25, C26: 100NF_50V_CER; C1206
C7, C9, C14, C16, C18, C27: 100UF_50V_ELE; C_P_3_5_8
D2, D3, D4, D5: 1N4148; D_DO-35_SOD27_P7.62mm_Horizontal
D6, D8, D10, D12: P6KE43CA; DIOAD1300W80L670D310
F1: TR5; FUSE_TR5
H1, H2, H3, H4: MountingHole_Pad_MP; MountingHole_3.5mm_Pad
L1, L2, L3, L4: Coil3; Coil3_100uH
PS1: AM2D-2405SZ; AM2D2405SZ
R1, R29: 910R; R3_5W
R2, R3, R5, R6: 10k; 1206
R4: 470R; 1206
R7, R8, R11, R12, R15, R16, R17, R18: 150k; 1206
R9, R13, R21, R23: 100R; R3_5W
R10, R14, R22, R24: 150R; R3_5W
R19, R20: 100R; 1206
R25, R26: 2.2k; R3_5W
R27: 0R; 1206
R28: 150R; 1206
ROW_VERT/1X1: ROW_VERT_1X8; ROW_VERT_1x8
SOCKET/1X1, SOCKET/1X2: SOCKET_1X2; SOCKET_1x2
TL431CLP1: TL431CLP_TO92; TO-92
TM_BLOCK/2P1, TM_BLOCK/2P2, TM_BLOCK/2P3: TM_BLOCK_2P
U1, U2: DFR0552
U3, U4: LM324NE4; DIP825W47P254L1917H533Q14

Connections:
5V: A1.27 (+5V), C2.1, C4.1, C6.1, C9.1, C14.1, C18.1, C19.1, D2.1 (K), D3.1 (K), PS1.6 (+V_OUT), R4.2, ROW_VERT/1X1.1
+24V: BC547_1.1 (C), BC547_2.1 (C), C5.1, C7.1, C8.1, C10.1, C13.1, C17.1, C25.1, C26.1, C27.1, F1.1, F1.2, PS1.1 (+Vin), R1.1, R25.2, TM_BLOCK/2P1.2, U3.4, U4.4
A0: A1.19 (A0), C22.1, D3.2 (A), D5.1 (K), R6.2
A1: A1.20 (A1), C21.1, D2.2 (A), D4.1 (K), R5.2
EncoderA: A1.5 (D2), ROW_VERT/1X1.7
EncoderB: A1.6 (D3), ROW_VERT/1X1.6
GND: Green1.1 (K), A1.4 (GND), A1.29 (GND), C2.2, C4.2, C5.2, C6.2, C7.2, C8.2, C9.2, C10.2, C11.1, C12.2, C13.2, C14.2, C15.1, C16.2, C17.2, C18.2, C19.2, C20.2, C21.2, C22.2, C25.2, C26.2, C27.2, D4.2 (A), D5.2 (A), D6.A, D8.A, D10.A, D12.A, PS1.2 (-Vin), PS1.4 (-V_OUT), R3.1, R4.1, R7.1, R10.1, R12.1, R22.1, ROW_VERT/1X1.2, ROW_VERT/1X1.8, SOCKET/1X1.2, SOCKET/1X2.2, TL431CLP1.2 (A), TM_BLOCK/2P1.1, U1.2 (GND), U2.2 (GND), U3.11, U4.11
unnamed: Green1.2 (A), R26.1
unnamed: BC547_1.2 (B), R19.2
unnamed: BC547_1.3 (E), R17.2, R23.2
unnamed: BC547_2.2 (B), R20.2
unnamed: BC547_2.3 (E), R13.2, R18.2
unnamed: C23.1, R7.2, R17.1, U3.2
unnamed: C23.2, R19.1, U3.1
unnamed: C24.1, R12.2, R18.1, U4.2
unnamed: C24.2, R20.1, U4.1
unnamed: D6.C, L1.1, R15.1, R24.1
unnamed: D8.C, L2.1, R14.1, R16.1
unnamed: D10.C, L3.1, R5.1, R9.2
unnamed: D12.C, L4.1, R6.1, R21.2
unnamed: R1.2, R29.1
unnamed: R2.1, R27.2
unnamed: R9.1, R10.2
unnamed: R11.2, R16.2, U4.3
unnamed: R13.1, R14.2
unnamed: R8.2, R15.2, U3.3
unnamed: R21.1, R22.2
unnamed: R23.1, R24.2
unnamed: R25.1, R26.2
unnamed: R3.2, R28.1
unnamed: R27.1, R28.2, TL431CLP1.1 (REF)
unnamed: L1.2, TM_BLOCK/2P2.1
unnamed: L3.2, TM_BLOCK/2P2.2
unnamed: L2.2, TM_BLOCK/2P3.1
unnamed: L4.2, TM_BLOCK/2P3.2
SCL: A1.24 (A5), ROW_VERT/1X1.3, U1.3 (SCL), U2.3 (SCL)
SDA: A1.23 (A4), ROW_VERT/1X1.4, U1.4 (SDA), U2.4 (SDA)
SW1: A1.7 (D4), ROW_VERT/1X1.5
V_DAC1: R8.1, SOCKET/1X1.1
V_DAC2: R11.1, SOCKET/1X2.1
Vref: A1.18 (AREF), C11.2, C12.1, C15.2, C16.1, C20.1, R2.2, R29.2, TL431CLP1.3 (K), U1.1 (VCC), U2.1 (VCC)

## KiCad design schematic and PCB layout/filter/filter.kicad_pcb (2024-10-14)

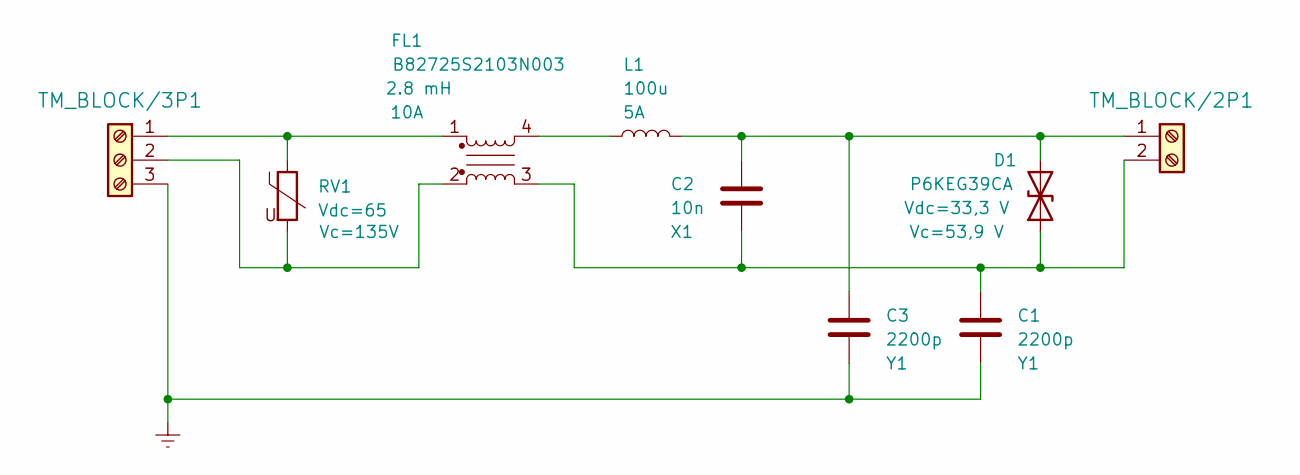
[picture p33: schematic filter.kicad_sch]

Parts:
C1, C3: 2200p; CAP_DE2E3SA222MJ3BT02F; Farnell 2507755
C2: 10n; CAPRB250W50L450T300H550; Farnell 2576736
D1: P6KEG39CA; DIOAD1995W86L635D340; Farnell 3226355
FL1: 2.8 mH; B82725S2103N003; Farnell 3580935
L1: 100u; PE92112KNL; Farnell 2215971
RV1: Vdc=65; B72220S0500K101; Farnell 1004301
TM_BLOCK/2P1: TM_BLOCK_2P
TM_BLOCK/3P1: TM_BLOCK_3P

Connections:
GNDREF: C1.2, C3.2, TM_BLOCK/3P1.3
unnamed: C1.1, C2.2, D1.1 (A1), FL1.3, TM_BLOCK/2P1.2
unnamed: C2.1, C3.1, D1.2 (A2), L1.2, TM_BLOCK/2P1.1
unnamed: FL1.4, L1.1
unnamed: FL1.1, RV1.1, TM_BLOCK/3P1.1
unnamed: FL1.2, RV1.2, TM_BLOCK/3P1.2

Board: 2 copper layers, 9 parts (0 on the bottom side), 6 nets, no tracks yet.

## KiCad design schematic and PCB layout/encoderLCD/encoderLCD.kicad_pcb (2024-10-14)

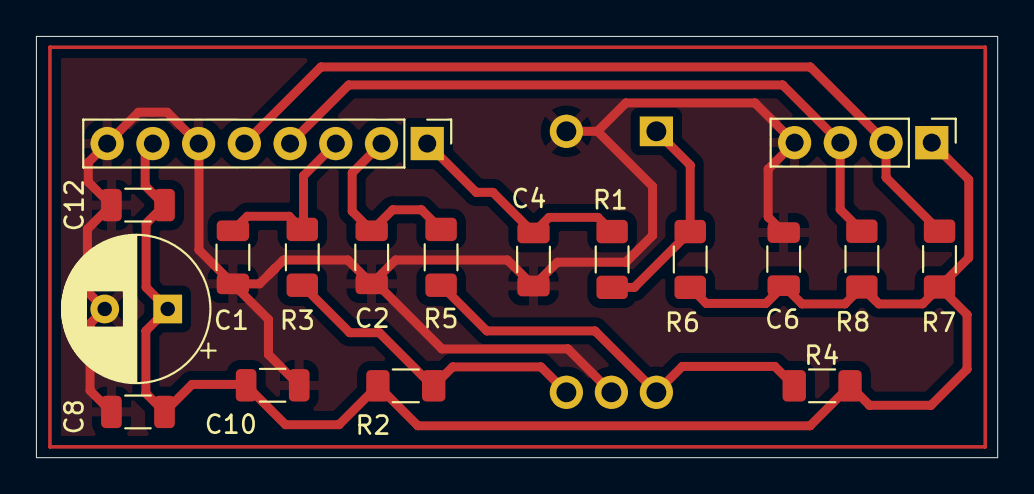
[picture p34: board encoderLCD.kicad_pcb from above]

Board: 2 copper layers, 53.4 x 23.4 mm, 19 parts (1 on the bottom side), 10 nets.

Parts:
C1, C2, C4: 10NF_50V_CER; C1206
C3: 100UF_50V_ELE; C_P_3_5_8
C6, C8, C10, C12: 100NF_50V_CER; C1206
R1, R2, R3, R4, R5, R6, R7, R8: 10k; 1206
ROW_VERT/1X1: ROW_VERT_1X4; ROW_VERT_1x4
ROW_VERT/1X2: ROW_VERT_1X8; ROW_VERT_1x8
SW1: Encoder; XDCR_PEC11R-4215F-S0024

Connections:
5V: C3.1, C6.1, C8.1, C10.1, C12.1, R2.1, R4.2, R6.1, R7.1, R8.1, ROW_VERT/1X1.1, ROW_VERT/1X2.7
EncoderA: C2.1, R5.2, ROW_VERT/1X2.2
EncoderB: C1.1, R3.2, ROW_VERT/1X2.3
GND: C1.2, C2.2, C3.2, C4.2, C6.2, C8.2, C10.2, C12.2, ROW_VERT/1X1.4, ROW_VERT/1X2.6, ROW_VERT/1X2.8, SW1.COM, SW1.S2
unnamed: R1.1, R6.2, SW1.S1
unnamed: R2.2, R3.1, SW1.B
unnamed: R4.1, R5.1, SW1.A
SCL: R8.2, ROW_VERT/1X1.3, ROW_VERT/1X2.4
SDA: R7.2, ROW_VERT/1X1.2, ROW_VERT/1X2.5
SW1: C4.1, R1.2, ROW_VERT/1X2.1

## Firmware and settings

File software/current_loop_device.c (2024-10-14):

/*	

	Software for two channel current loop device

	Calibration:
	Adjust DAC output so that current in multimeter 
	Fluke shows 20 mA and record DAC ja ADC values
	repeat this for both channels.

*/

//#include <Wire.h>

//comment this Adafruit for real device
//#include "Adafruit_LiquidCrystal.h"


// for real device
#include <Wire.h>
#include "DFRobot_MCP4725.h"
#include <LiquidCrystal_I2C.h>
#include <avr/wdt.h> //Watchdog Timer library

//comment this Adafruit for real device
//Adafruit_LiquidCrystal lcd(0x20);  // set the LCD address to 0x20 for a 16 chars and 2 line display

// for real device 
DFRobot_MCP4725 DAC1;
DFRobot_MCP4725 DAC2;
LiquidCrystal_I2C lcd(0x27,16,2); //I2C address 0x27, 16 column and 2 rows


void write_lcd(float torgue, int rpm, bool dac_select, int error);
void write_dac(float torgue, int rpm);
void init_lcd(void);
void ISR_pushButton(void);
void ISR_encoderChange(void);
int open_loop_error_check(void);
//void print_all_values_to_serial_terminal(float torgue, int rpm, bool dac_select);

#define CLK_PIN 2 //encoder A output
#define DT_PIN 3  //encoder B output
#define SW_PIN 4  //encoder switch pin
#define limit_for_fast_increment_in_ms 100 //time limit in milliseconds before encoder values are read faster
#define calibration_value_for_ADC_ch0 1023 //this is tested when loop current accurately 20.0 mA
#define calibration_value_for_ADC_ch1 1023 //this is tested when loop current accurately 20.0 mA
#define calibration_value_for_DAC_ch0 5000 //this is tested when loop current accurately 20.0 mA
#define calibration_value_for_DAC_ch1 5000 //this is tested when loop current accurately 20.0 mA
#define REF_VOLTAGE1 5135.0 //uncomment for real device, update the actual voltage measured by multimeter
#define REF_VOLTAGE2 5044.0 //uncomment for real device, update the actual voltage measured by multimeter

#define maximum_value_for_torgue 50.00
#define step_for_torgue 0.50
#define minimum_step_for_torgue 0.05
#define maximum_value_for_rpm 3000
#define step_for_rpm 30
#define minimum_step_for_rpm 3

//global variables
bool DAC_select=0;
float torgue=0;
int rpm=0;

void setup()
{
     //uncommetn thise for real device
    Wire.begin(); 
    lcd.init(); 
    lcd.backlight(); 
    
    DAC1.init(MCP4725A0_IIC_Address0, REF_VOLTAGE1);  //DAC1
    DAC2.init(MCP4725A0_IIC_Address1, REF_VOLTAGE2);  //DAC2
    DAC1.outputVoltage(0.0);
    DAC2.outputVoltage(0.0);
	
    Serial.begin(115200);
    
    pinMode(SW_PIN,INPUT);
	  pinMode(DT_PIN,INPUT);
	  pinMode(CLK_PIN,INPUT);
	  delay(100);
	  //lcd.begin(16, 2); //comment this for real divice
	  init_lcd(); //initalize LCD so that values are 0
    Serial.println("setup ready");
	  delay(1000);
	  attachInterrupt(digitalPinToInterrupt(DT_PIN), ISR_encoderChange, CHANGE);
	  attachInterrupt(digitalPinToInterrupt(CLK_PIN), ISR_encoderChange, CHANGE); 
    wdt_enable(WDTO_1S);  //Enable watchdog timer with a timeout of 1 second

}

void loop()
{
  wdt_reset(); 
 	//interrupt reads values for torgue and rpm from rotary encoder
	//interrupt reads DAC_select so values 0 or 1
	int error=open_loop_error_check(); //check if current loop ok
	write_lcd(torgue,rpm,DAC_select,error); //writes torgue, rpm values for LCD and DAC_selec asterisk
	write_dac(torgue,rpm); //write values to the real DAC and current loop output
	print_all_values_to_serial_terminal(torgue,rpm,DAC_select);
  read_push_button_state();
}


void init_lcd(void)
{
	lcd.setCursor(0, 0);
	lcd.print("     ");
	lcd.setCursor(0, 0);
	lcd.print(torgue);
	lcd.setCursor(6, 0);
	lcd.print("Nm");

	lcd.setCursor(0, 1);
	lcd.print("     ");
	lcd.setCursor(0, 1);
	lcd.print(rpm);
	lcd.setCursor(6, 1);
	lcd.print("rpm");

	if(DAC_select==0)
	{
		lcd.setCursor(12, 1);
		lcd.print(" ");
		lcd.setCursor(12, 0);
		lcd.print("*");
	}
	else
	{
		lcd.setCursor(12, 0);
		lcd.print(" ");
		lcd.setCursor(12, 1);
		lcd.print("*");
	}	
}




void write_lcd(float torgue, int rpm, bool DAC_select, int error)
{

	static float old_torgue=0;
	static int old_rpm=0;
	static bool old_DAC_select=0;
	static int error_old=0;

	if(torgue!=old_torgue||error!=error_old) //write only if value changed or error status changed
	{
		lcd.setCursor(0, 0);
		lcd.print("     ");
		lcd.setCursor(0, 0);
		if(error==0||error==2)
			lcd.print(torgue);
		else if(error==1||error==3)
			lcd.print("OL"); //error = 1 or 3 so open loop in torgue channel
		lcd.setCursor(6, 0);
		lcd.print("Nm");
	}

	if(rpm!=old_rpm||error!=error_old) //write only if value changed or error status changed
	{
		lcd.setCursor(0, 1);
		lcd.print("     ");
		lcd.setCursor(0, 1);
		if(error==0||error==1)
			lcd.print(rpm);
		else if(error==2||error==3) //error = 2 or 3 so open loop in rpm channel
			lcd.print("OL");
		lcd.setCursor(6, 1);
		lcd.print("rpm");
	}

	if(DAC_select!=old_DAC_select) //write only if value changed
	{
		if(DAC_select==0)
		{
			lcd.setCursor(12, 1);
			lcd.print(" ");
			lcd.setCursor(12, 0);
			lcd.print("*");
		}
		else
		{
			lcd.setCursor(12, 0);
			lcd.print(" ");
			lcd.setCursor(12, 1);
			lcd.print("*");
		}
	}

	//store old values to static variables
	old_torgue=torgue;
	old_rpm=rpm;
	old_DAC_select=DAC_select;
	error_old=error;
}



void read_push_button_state(void) //if push-button pressed on encoder
{
    static long timex=0;

    if(digitalRead(SW_PIN)==0&&millis()>timex+200)
	  {
        DAC_select=!DAC_select;
        timex=millis();
    }
}

void ISR_encoderChange(void)
{

//https://www.youtube.com/watch?v=fgOfSHTYeio

static unsigned long _lastIncReadTime = micros(); 
static unsigned long _lastDecReadTime = micros(); 
int _pauseLength = 25000;

  // Encoder interrupt routine for both pins. Updates counter
  // if they are valid and have rotated a full indent
 
  static uint8_t old_AB = 3;  // Lookup table index
  static int8_t encval = 0;   // Encoder value  
  static const int8_t enc_states[]  = {0,-1,1,0,1,0,0,-1,-1,0,0,1,0,1,-1,0}; // Lookup table

  old_AB <<=2;  // Remember previous state

  if (digitalRead(CLK_PIN)) old_AB |= 0x02; // Add current state of pin A
  if (digitalRead(DT_PIN)) old_AB |= 0x01; // Add current state of pin B
  
  encval += enc_states[( old_AB & 0x0f )];

  // Update counter if encoder has rotated a full indent, that is at least 4 steps
  if( encval > 3 ) 
  {        // Four steps forward

    if((micros() - _lastIncReadTime) < _pauseLength) 
    {
      if(DAC_select==1&&rpm<=(maximum_value_for_rpm-step_for_rpm))
				rpm=rpm+step_for_rpm;
			else if(DAC_select==1&&rpm>(maximum_value_for_rpm-step_for_rpm))
				rpm=maximum_value_for_rpm;

      if(DAC_select==0&&torgue<=(maximum_value_for_torgue-step_for_torgue))
				torgue=torgue+step_for_torgue;
			else if(DAC_select==0&&torgue>(maximum_value_for_torgue-step_for_torgue))
				torgue=maximum_value_for_torgue;	
    }
    else
    {
      if(DAC_select==1&&rpm<=(maximum_value_for_rpm-minimum_step_for_rpm))
				rpm=rpm+minimum_step_for_rpm;
      
      if(DAC_select==0&&torgue<=(maximum_value_for_torgue-minimum_step_for_torgue))
				torgue=torgue+minimum_step_for_torgue;
    }
    _lastIncReadTime = micros();
 
    encval = 0;
  }
  else if( encval < -3 ) 
  {        // Four steps backward

    if((micros() - _lastDecReadTime) < _pauseLength) 
    {
			if(DAC_select==1&&rpm>=step_for_rpm)
				rpm=rpm-step_for_rpm;
			else if(DAC_select==1&&rpm<step_for_rpm)
				rpm=0;
      
      if(DAC_select==0&&torgue>=step_for_torgue)
				torgue=torgue-step_for_torgue;
      else if(DAC_select==0&&torgue<step_for_torgue)
				torgue=0;
    }
    else
    {
			if(DAC_select==1&&rpm>=minimum_step_for_rpm)
				rpm=rpm-minimum_step_for_rpm;

      if(DAC_select==0&&torgue>=minimum_step_for_torgue)
				torgue=torgue-minimum_step_for_torgue;
    }
    _lastDecReadTime = micros();
    encval = 0;
  }
  
		if(torgue>=maximum_value_for_torgue) //for safety 
			torgue=maximum_value_for_torgue;
		else if(torgue<0)
			torgue=0;

		if(rpm>=maximum_value_for_rpm) //for safety
			rpm=maximum_value_for_rpm;
		else if(rpm<0)
			rpm=0;

}

void write_dac(float torgue, int rpm)
{
	static int rpm_old=0;
	static float torgue_old=0;

	if(rpm!=rpm_old) //if different than old value
	{
		//for example calibrated value 4087 and wanted 3000 rpm so 4087/3000*3000=4087
		int dac_rpm=(float)calibration_value_for_DAC_ch1/maximum_value_for_rpm*rpm;
        //here real DAC write
        DAC2.outputVoltage(dac_rpm);	
	}

	if(torgue!=torgue_old) //if different than old value
	{
        //for example calibrated value 4081 and wanted 50.00 torgue so 4081/50*50=4081
		int dac_torgue=(float)calibration_value_for_DAC_ch0/maximum_value_for_torgue*torgue;
        //here real DAC write
        DAC1.outputVoltage(dac_torgue);	
	}
	torgue_old=torgue;
	rpm_old=rpm;
}

int open_loop_error_check(void)
{
	//calculates feedback value from ADC (torgue and rpm) and scales to 0-4095
	int feedback_adc_value_for_torgue=(float)calibration_value_for_DAC_ch0/calibration_value_for_ADC_ch0*analogRead(A0);
	int feedback_adc_value_for_rpm=(float)calibration_value_for_DAC_ch1/calibration_value_for_ADC_ch1*analogRead(A1);
	int error_ch0=0;
	int error_ch1=0;

	//calculates comparable DAC value from wanted torgue and scales to 0-4095
	int dac_value_for_torgue=(float)calibration_value_for_DAC_ch0/maximum_value_for_torgue*torgue;
	
	//calculates comparable DAC value from wanted rpm and scales to 0-4095
	int dac_value_for_rpm=(float)calibration_value_for_DAC_ch1/maximum_value_for_rpm*rpm;

	//if wanted torgue > 100/4095*5V=0,122V and feeback less than 20/4095*5V=0,024V gives alarm
	if(dac_value_for_torgue>100&&feedback_adc_value_for_torgue<20)
		error_ch0=1; //maybe open loop error in CH0

	//if wanted rpm > 100/4095*5V=0,122V and feeback less than 20/4095*5V=0,024V gives alarm
	if(dac_value_for_rpm>100&&feedback_adc_value_for_rpm<20)
		error_ch1=2; //open loop error in CH1

	/*
	error = 1 torgue channel error
	error = 2 rpm channel error
	eroor = 3 torgue and rpm channel error	
	*/

	return (error_ch0+error_ch1);
}

void print_all_values_to_serial_terminal(float torgue, int rpm, bool dac_select)
{
    static int rpm_old=0;
	static float torgue_old=0;
    static bool old_DAC_select=0;

	if(rpm!=rpm_old) //if different than old value
	    {
        int dac_rpm=(float)calibration_value_for_DAC_ch1/maximum_value_for_rpm*rpm;
		Serial.print("RPM 0-3000:");
		Serial.println(rpm);
		Serial.print("DAC rpm 0-5000:");
		Serial.println(dac_rpm);
        }
    
    if(torgue!=torgue_old) //if different than old value
	    {        
        int dac_torgue=(float)calibration_value_for_DAC_ch0/maximum_value_for_torgue*torgue;
        Serial.print("Torgue 0-50.00:");
		Serial.println(torgue);	
		Serial.print("DAC torgue 0-5000:");
		Serial.println(dac_torgue);		
        }

    if(DAC_select!=old_DAC_select) //write only if value changed
	    {
        Serial.print("DAC select: ");
		Serial.println(DAC_select);
        }

        torgue_old=torgue;
	    rpm_old=rpm;
        old_DAC_select=DAC_select;
}
